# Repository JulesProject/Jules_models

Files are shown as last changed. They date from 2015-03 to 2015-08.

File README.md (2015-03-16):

# README

## Abstract
Jules is a project started in February 2015. The aim of this project is to design a robot to help elementary and kindergaten teachers in there everyday jobs. 

Jules is designed to be safe for kids, nice looking and usefull for their teachers. Jules must be suitable to kids from 5 to 9 years old and propose differents scenarios for them too.

## Folders Structure

The Models folder contains all SolidWorks models (created with SolidWorks 2013). The Printing models are STL files designed to be printed with 3D printers.

* README
* models
    * accessories 
        * arms
        * feet
            * first_edition
            * second_edition
        * tail  
    * body   
        * neck
        * ballast
    * electronics   
        * ballBearing1
        * dynamixels
    * head  
        * antenna
* printing
    * antenna  
    * arms  
    * body  
    * feet  
    * head  
    * neck
    * ballast
    * tail

## Components

The components listed here are components we designed our solution for. 
Not all the components are required to create a first version of the robot.

#### Head components
* Camera - [LogitechC920]
* Actuator Dynamixel RX-24f - [Dynamixel]
* Screen + TouchScreen - HDMI+VGA+2AV Controller Board VS-TY2662-V1 7 inch 800* 480  Lcd Panel AT070TN92 with Touch Screen  
    * USB Controller Card
    * USB Cable
* Speakers Monacor SPP-90 - [Speakers]
    * Audio amplifier - [Amplifier]
* Actuator to card transformer - [USB2Dynamixel]
* Electronic card + Heat sink - [BananaPi]

#### Body components
* Microphone - [Boya]
* Actuator - [Dynamixel]
* On/Off button
* Ultrasound card - HC-SR04

#### Other mendatory materials
* Ball bearing (x1) - [BallBearing1]
* Ball bearing (x2) - [BallBearing2]
* Power supply cable 12V 3A
* Power supply socket 
* Power converter (12V to 5V) - DC-DC 12V/ 24V to 5V 5A Step Down Regulator Module 25W Converter
* Power usb plug - Male B type Version 2.0 Micro USB Connector, 100 V ac, 1.8A
* SD card - 32Gb class 10
* Dynamixel cables - 4-pin
* ProtoBoard - [ProtoBoard]
* Resistor 470 ohm
* Resistor 330 ohm
* Wires
* Soldering iron
* Screws

[LogitechC920]:http://www.logitech.com/en-hk/product/hd-pro-webcam-c920
[Dynamixel]: http://en.robotis.com/index/product.php?cate_code=10101112&bbs_no=29#product_title
[Speakers]:http://www.monacor.co.uk/products/speakerbuilding-hifi-4/vnr/101150/
[USB2Dynamixel]:http://support.robotis.com/en/product/auxdevice/interface/usb2dxl_manual.htm
[BananaPi]:http://bananapi.com/index.php/component/content/article?layout=edit&id=73
[Boya]:http://www.boya-mic.com/products/show-394.html
[BallBearing1]:http://www.skf.com/uk/products/bearings-units-housings/ball-bearings/deep-groove-ball-bearings/single-row-deep-groove-ball-bearings/single-row/index.html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
[BallBearing2]:http://www.skf.com/uk/products/bearings-units-housings/ball-bearings/deep-groove-ball-bearings/single-row-deep-groove-ball-bearings/single-row/index.html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
[Amplifier]:https://learn.adafruit.com/adafruit-ts2012-2-8w-stereo-audio-amplifier/overview

## Printing

All the parts can be printed on a 3D printer with at least a 18x18x18cm plateau (originally designed to be printed with a Ultimaker printer). 

It is needed around 3kg of material to be able to print the full robot. 
Arms, feet, antenna, tail are designed to be printed in another color than the rest of the robot.

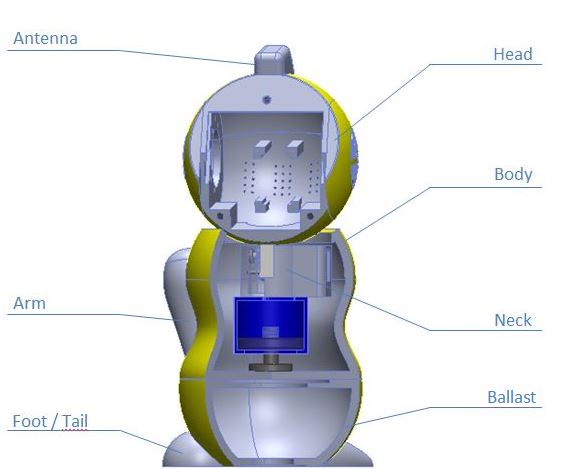
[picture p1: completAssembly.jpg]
Root complete Assembly


Two versions of the feet are available. For the second version, the tail file is needed as well to insure the stability of the robot.

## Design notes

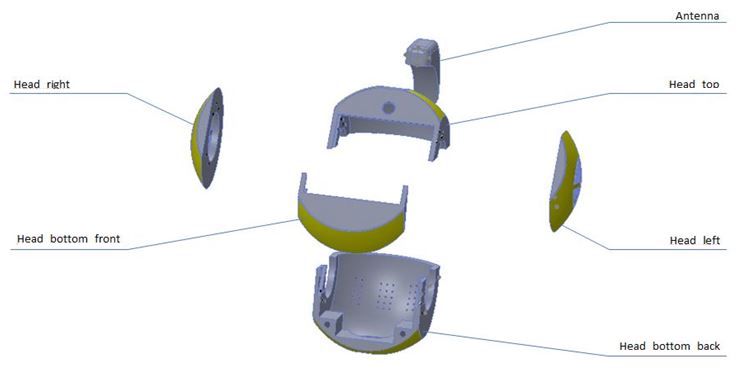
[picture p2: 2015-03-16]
models/head/head.JPG

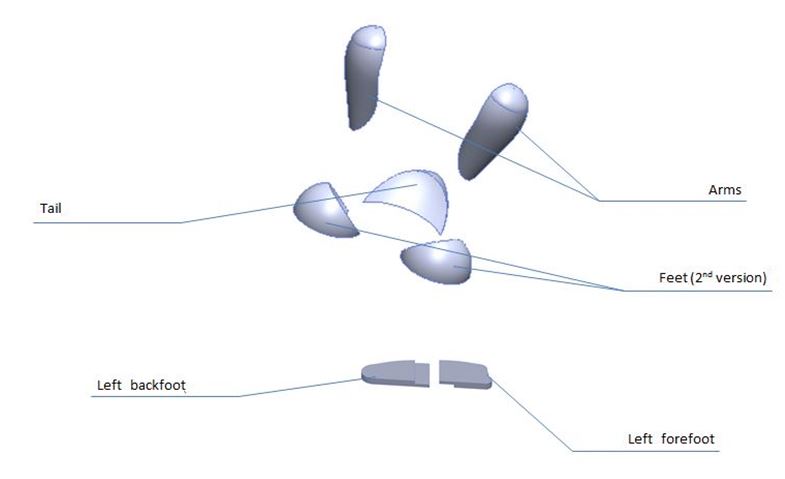
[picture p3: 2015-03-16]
models/accessories/accessories.JPG

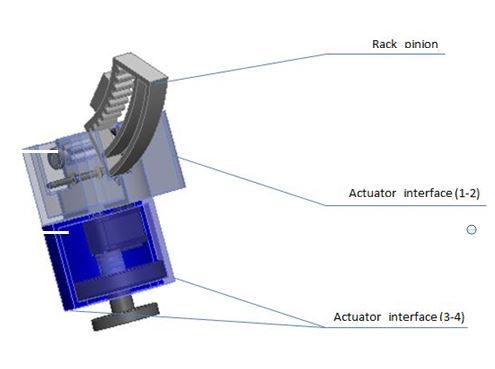
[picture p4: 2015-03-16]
models/body/neck/neck.JPG

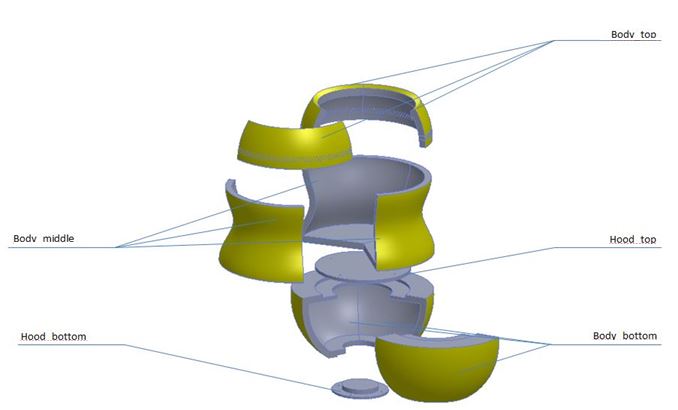
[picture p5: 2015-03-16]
models/body/body.JPG

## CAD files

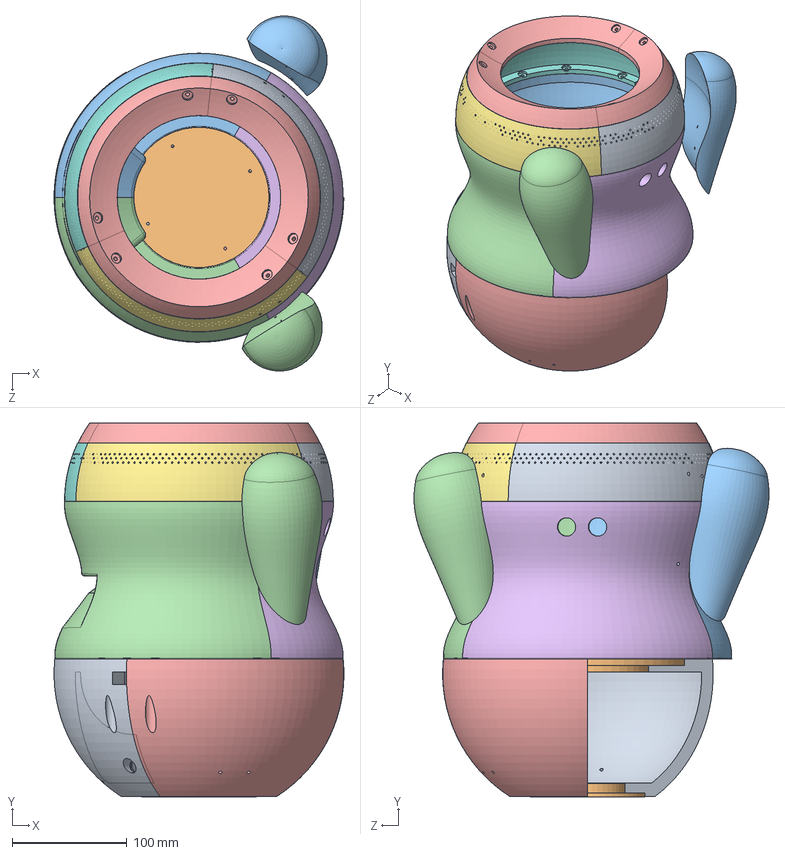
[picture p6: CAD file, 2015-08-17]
models/body/bodyAssembly.SLDASM
252.0 x 325.0 x 308.7 mm
body_bottom_back
hood_bottom
body_middle_handle_left
body_middle_handle_right
body_bottom_left
body_middle_front
body_top_left
body_top_middle
body_top_right
hood_top
right_arm
left_arm
body_top_hood x 3

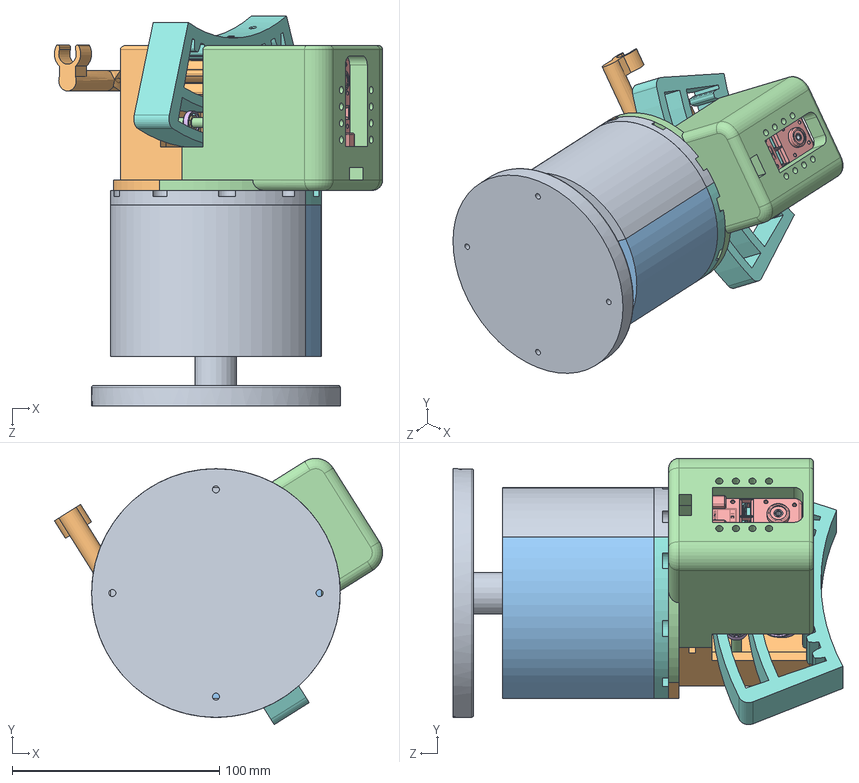
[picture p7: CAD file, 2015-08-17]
models/body/neck/neck.sldasm
158.4 x 128.5 x 188.2 mm
actuator_interface_3
actuator_interface_2
actuator_interface_4
actuator_interface_1
ASSY_DUMMY___^AX-18A
ASSY_GEAR-WHEEL___DUMMY^AX-18A
DX124_SCREW-COVER___^AX-18A x 4
099990987____^AX-18A x 2
DC04_B01_INSERT_M3^AX-18A
DC04_B01_HORN2_DUMMY^AX-18A
BHS_M2_6X8^AX-18A
neck_axis x 2
ball1 x 2
ball2 x 2
ball3 x 2
ball4 x 2
ball5 x 2
ball6 x 2
ball7 x 2
ball8 x 2
ball9 x 2
external_ring x 2
internal_ring x 2
rack_pinion
sprocket_2
sprocket_1
AX-12A-01
AX-12A-02
AX-12A-03
AX-12A-04
SetScrew x 4
M2.5 x 8
actuator_holder
actuator_axis
ball
ball_2
ball_3
ball_4
ball_5
ball_6
ball_7
ball_8
ball_9
ball_10
ball_11
external_bearing_ring
internal_bearing_ring
actuator_interface_3_handle
actuator_interface_4_handle
handle_microphone

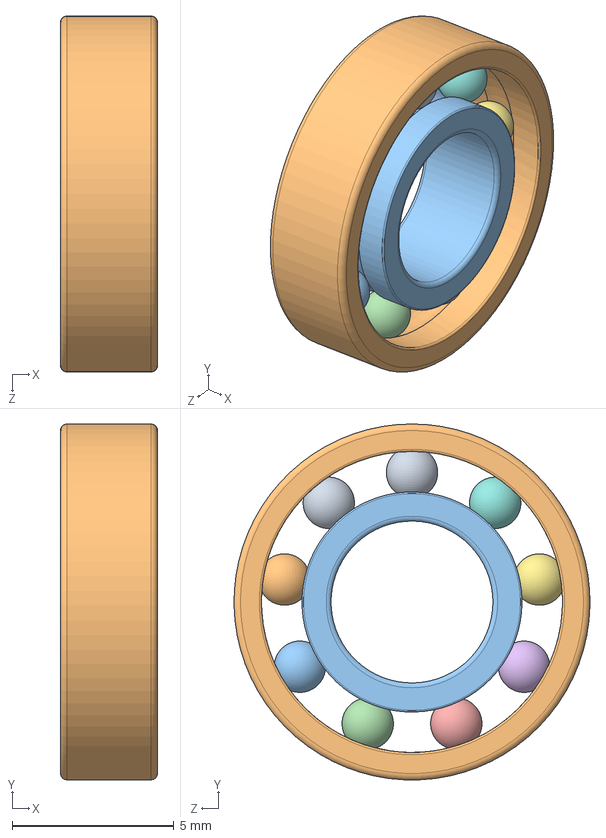
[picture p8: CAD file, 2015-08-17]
models/electronics/ballBearing1/ballBearing.SLDASM
3.00 x 11.0 x 11.0 mm
ball1
ball2
ball3
ball4
ball5
ball6
ball7
ball8
ball9
external_ring
internal_ring

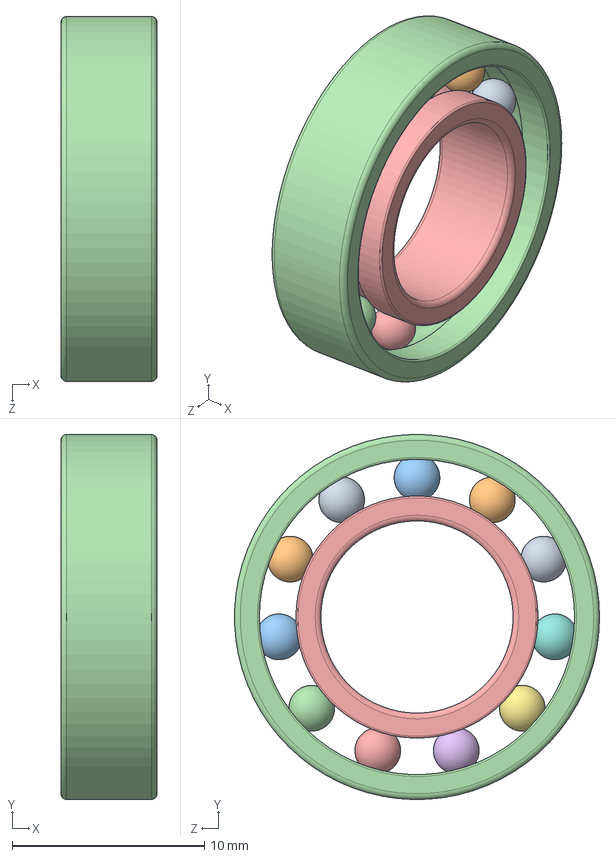
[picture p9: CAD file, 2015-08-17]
models/electronics/ballBearing2.sldasm
5.00 x 19.0 x 19.0 mm
ball
ball_2
ball_3
ball_4
ball_5
ball_6
ball_7
ball_8
ball_9
ball_10
ball_11
external_bearing_ring
internal_bearing_ring

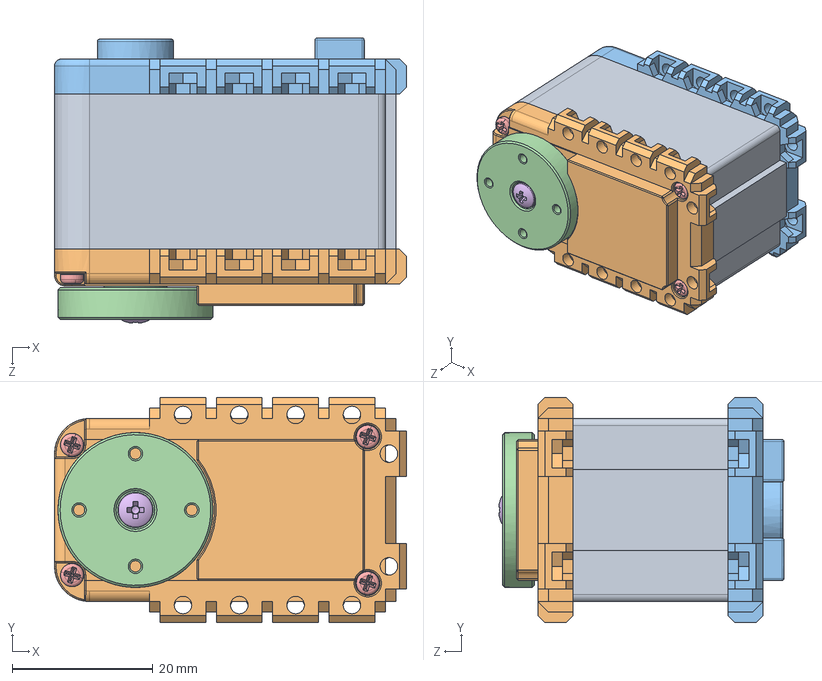
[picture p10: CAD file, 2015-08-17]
models/electronics/dynamixels/DYNAMIXEL AX-12A.SLDASM
50.0 x 32.0 x 40.5 mm
AX-12A-01
AX-12A-02
AX-12A-03
AX-12A-04
SetScrew x 4
M2.5 x 8

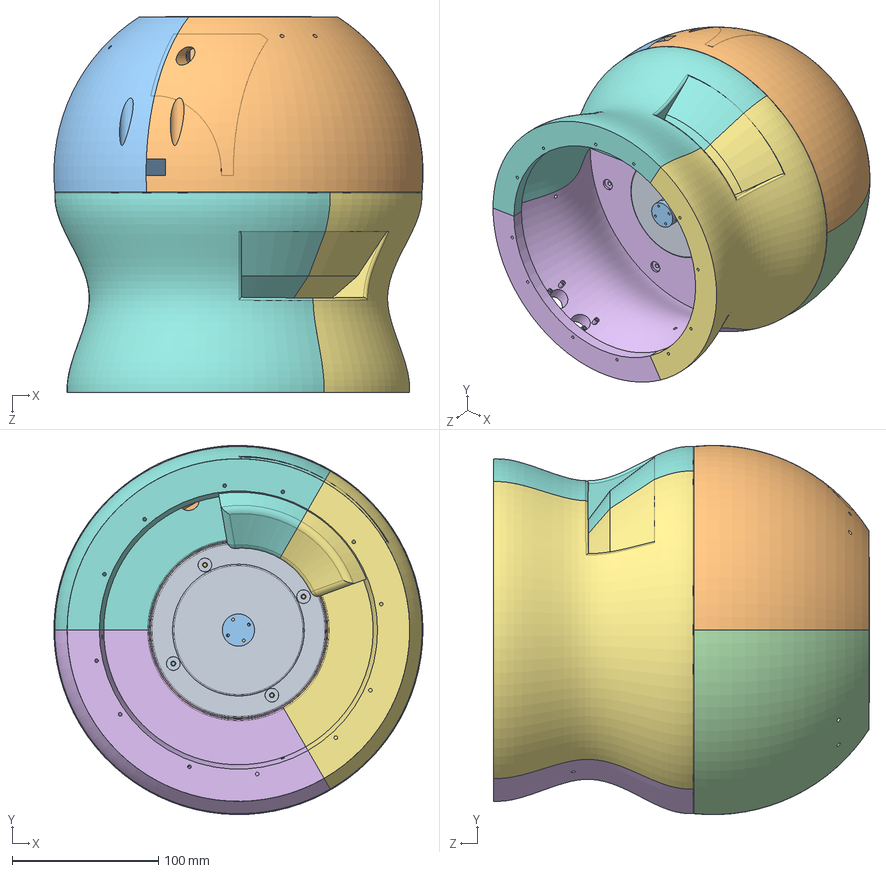
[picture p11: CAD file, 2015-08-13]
models/finalAssembly2.SLDASM
252.0 x 252.1 x 257.1 mm
hood_bottom
body_bottom_back
body_bottom_left
body_bottom_right
hood_top
body_middle_front
body_middle_handle_left
body_middle_handle_right
actuator_holder
sprocket_2
sprocket_1

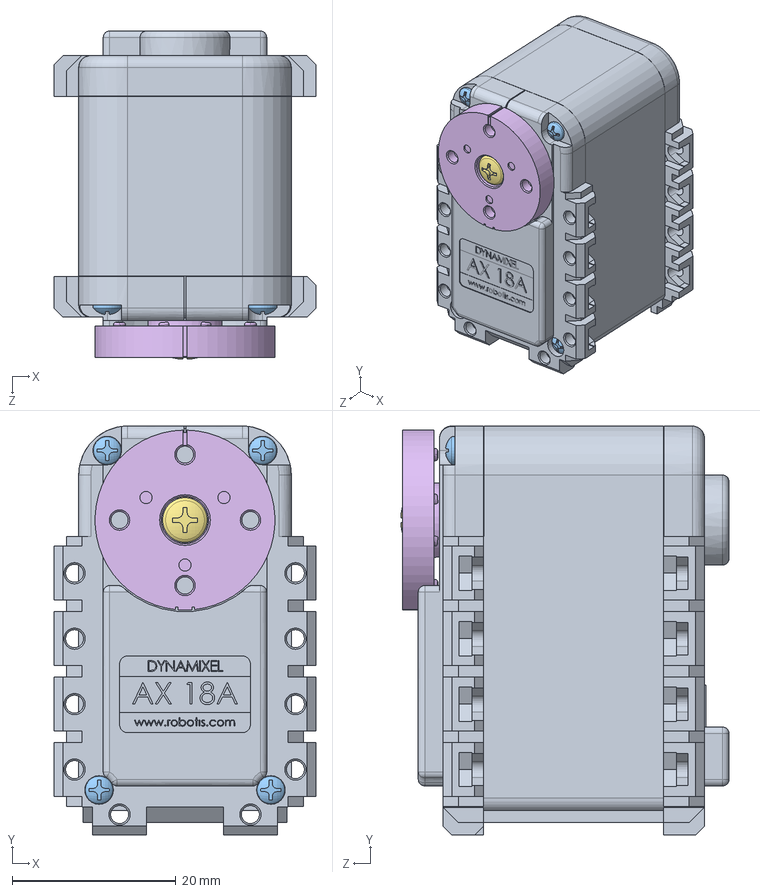
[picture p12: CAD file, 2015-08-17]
models/electronics/dynamixels/AX-18A.SLDASM
32.0 x 50.0 x 40.1 mm
ASSY_DUMMY___^AX-18A
ASSY_GEAR-WHEEL___DUMMY^AX-18A
DX124_SCREW-COVER___^AX-18A x 4
099990987____^AX-18A x 2
DC04_B01_INSERT_M3^AX-18A
DC04_B01_HORN2_DUMMY^AX-18A
BHS_M2_6X8^AX-18A

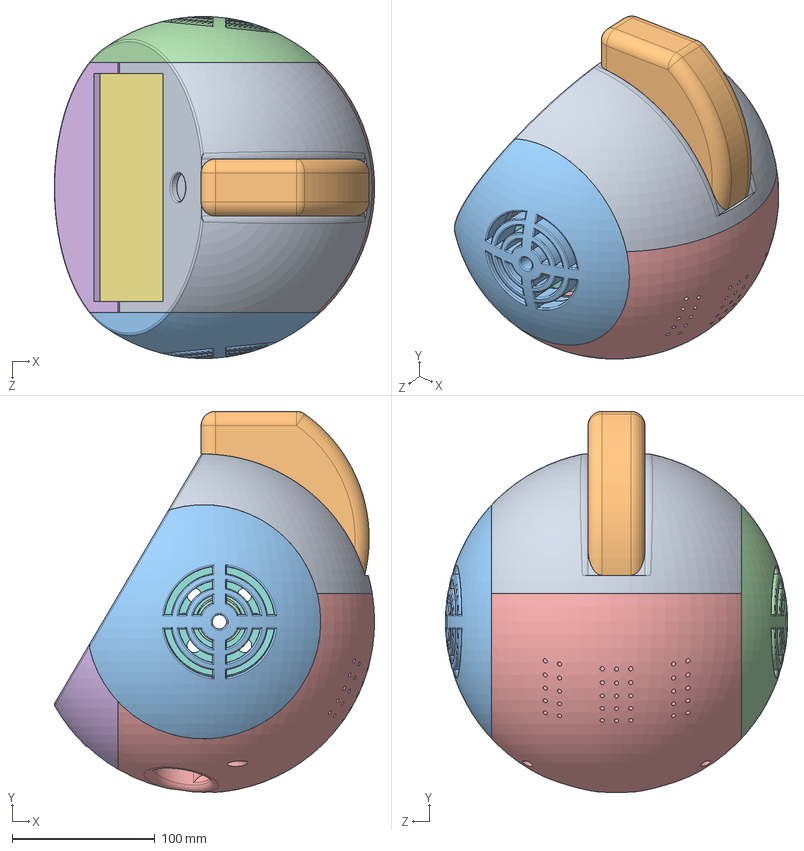
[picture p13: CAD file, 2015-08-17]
models/head/fullHead.SLDASM
224.5 x 267.4 x 239.9 mm
head_top
antenna
head_right
head_left
head_bottom_back
head_bottom_front
screen_ts
speaker_holder x 2
logitech_webcam
webcam_holder

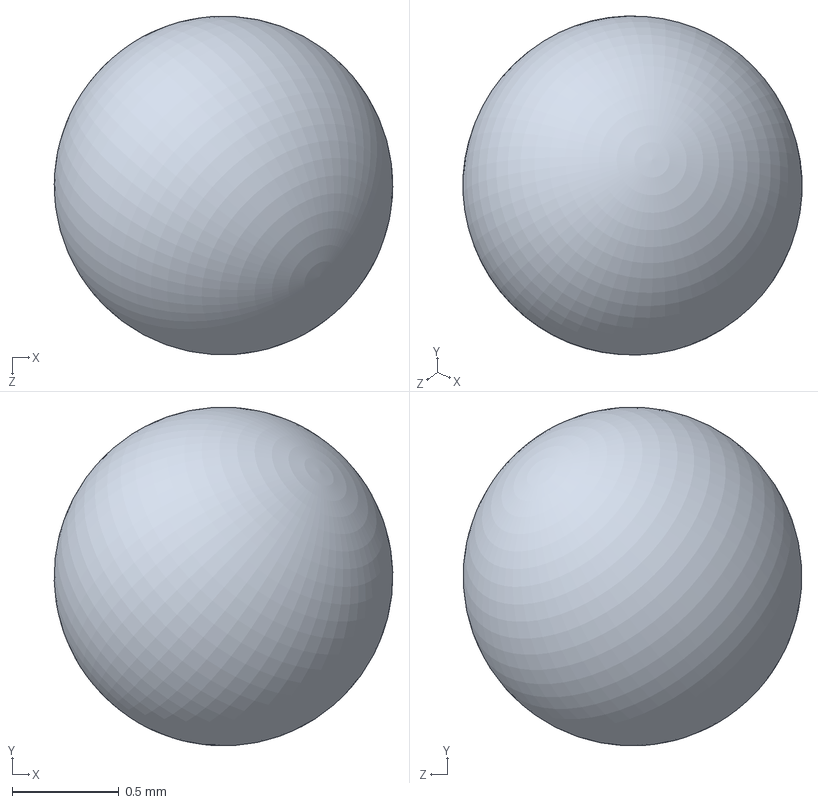
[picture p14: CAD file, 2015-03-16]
models/electronics/dynamixels/4_PART_618_5_PART3_in_ASM_618_5.sldprt
1.59 x 1.59 x 1.58 mm

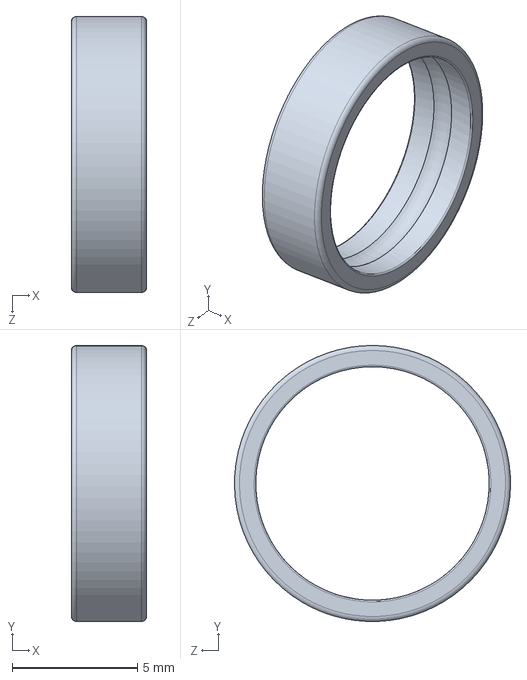
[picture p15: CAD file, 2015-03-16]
models/electronics/dynamixels/10_PART_618_5_PART3_in_ASM_618_5.sldprt
3.00 x 11.0 x 11.0 mm

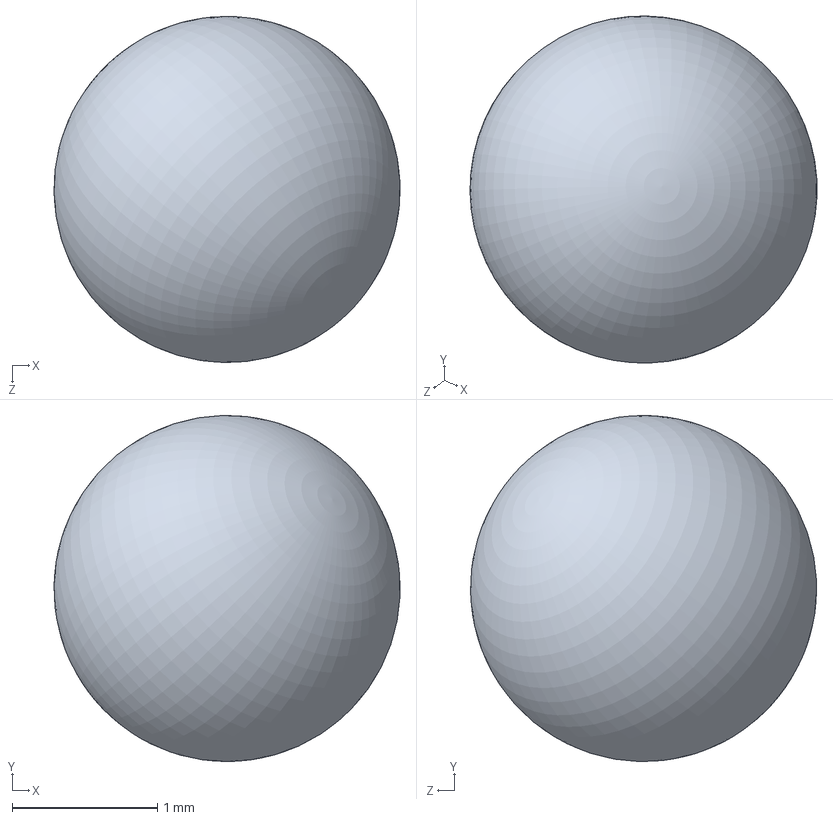
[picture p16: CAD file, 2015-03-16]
models/electronics/dynamixels/5_PART_61800_PART3_in_ASM_61800.sldprt
2.38 x 2.38 x 2.38 mm

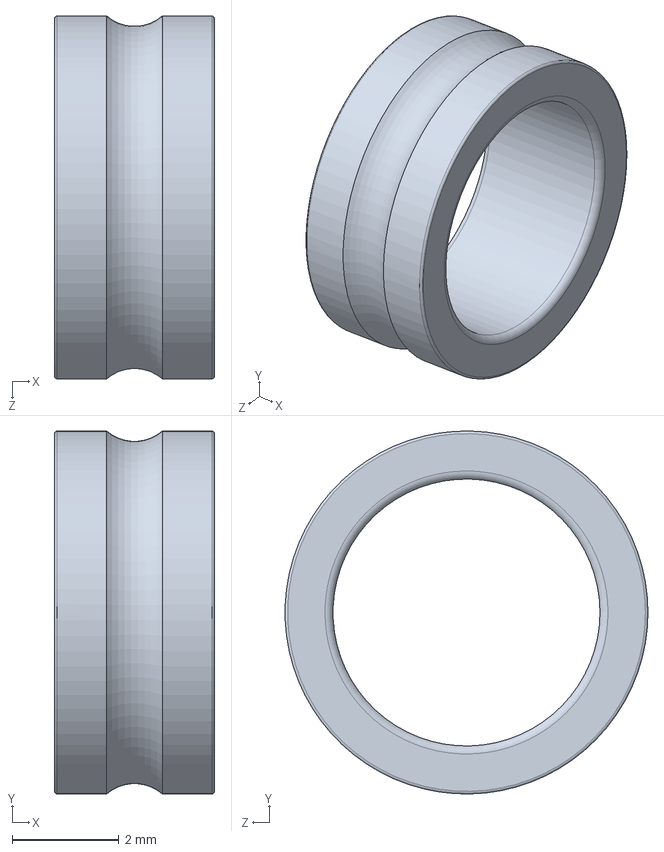
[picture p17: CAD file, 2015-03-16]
models/electronics/dynamixels/11_PART_618_5_PART3_in_ASM_618_5.sldprt
3.00 x 6.80 x 6.80 mm

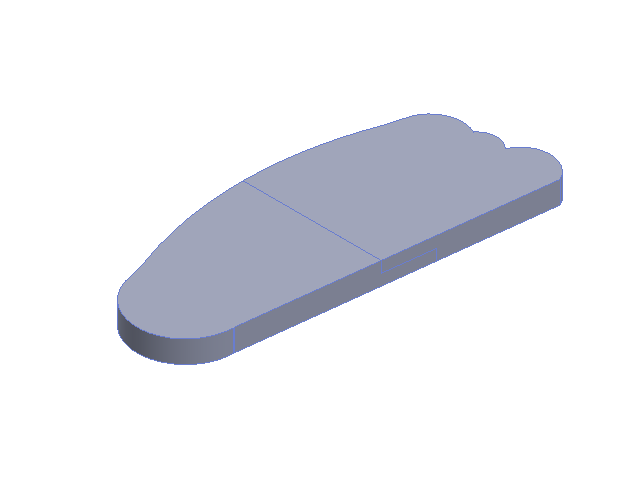
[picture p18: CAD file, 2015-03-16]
models/accessories/feet/first_edition/left_foot.SLDASM
left_forefoot
left_backfoot

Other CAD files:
models/electronics/dynamixels/2_PART_618_5_PART2_in_ASM_618_5.sldprt
models/electronics/dynamixels/1_PART_618_5_PART1_in_ASM_618_5.sldprt
models/electronics/dynamixels/7_PART_618_5_PART3_in_ASM_618_5.sldprt
models/electronics/dynamixels/4_PART_61800_PART3_in_ASM_61800.sldprt
models/electronics/dynamixels/6_PART_61800_PART3_in_ASM_61800.sldprt
models/accessories/arms/left_arm.SLDPRT
models/accessories/arms/right_arm.SLDPRT
models/accessories/feet/first_edition/left_backfoot.SLDPRT
models/accessories/feet/first_edition/left_forefoot.SLDPRT
models/accessories/feet/second_edition/left_foot.SLDPRT
models/accessories/feet/second_edition/right_foot.SLDPRT
models/accessories/tail/tail.SLDPRT
models/body/ballast/body_bottom_back.SLDPRT
models/body/ballast/body_bottom_left.SLDPRT
models/body/ballast/body_bottom_right.SLDPRT
models/body/ballast/hood_bottom.SLDPRT
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

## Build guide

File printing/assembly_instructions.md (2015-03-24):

# Instructions for assembly

Assembly video : 
[Assembly video](http://youtu.be/b8QJ62R7ehc)

## The body assembly

### The first version feet assembly

Need:
* Plastic parts:
* Backfoot x2
* Forefoot x2

First, take the forefoot and backfoot of one of your feet.
Screw the external screw of the foot from the bottom of this one.

Repeat with your second foot.

### The ballast assembly

Need: 
* Plastic parts:
* Body bottom x1
* Body bottom with switch and power supply cable x1
* Body bottom with internal hood x1
* Hood top x1
* Hood bottom x1
* Foot x2
* Electronics:
* Switch x1
* Power supply cable x1
* Power supply plug x1
* Other
* Bag food of iron x1

Take the body bottom with the holes for the switch and power supply plug.
Fix the switch and weld it.
Fix the power plug and weld it as well.

Take the body bottom with the internal hood and screw it on the right part of previous piece

Take the bottom hood and screw it on one of the body bottom top part.
Do the same with the two other bottom's parts.

Put the bag food of iron inside of the structure and screw the top hood to the structure.

Take one of your feet, return the ballast and screw it.
Repeat the same with the second foot.

### The middle body assembly

Need:
* Plastic parts:
* Ballast assembly x1
* Body front middle (with ultrasound holes) x1
* Body middle (with left handle) x1

Take the ballast assembly and screw one of the middle body on it. 
Repeat the same with the two other middle body parts.

### The neck assembly

Need:
* Plastic parts:
* Middle body assembly x1
* Neck x1
* Electronics:
* Dynamixel RX-24f x2
* Microphone x1

Take the middle body assembly and screw on it (in the middle of the structure, inside the middle parts), the neck.

### The middle body

Need:
* Plastic parts:
* Body assembly x1
* Body middle (with right handle) x2

Screw the two middle parts to the robot thanks to the holes in the back of it.

### The upper body assembly

Need:
* Plastic parts:
* Neck assembly
* Body top x3
* Body hood x3
* Arm x2
* Neck hood x1
* Electonics:
* Ultrasound card x1

Screw an arm to each of the body top parts.
Take the two body top parts and screw them together thanks to the two screws holes integrated.

Screw this structure to the whole assembly done before.

Plug the ultrasound card to the body top front and screw it.

Position the body top front on the top of the structure, next to the two other body top parts.
Don't forget to make all the cables getting out of the neck.
Add the neck hood on top of it and screw the structure together.

## The head assembly 

### The top of the head

Need: 
* Plastic parts:
* Forehead x1
* Antenna x1
* Camera hood x1
* Electronics:
* Camera x1

Take the forehead and screw the antenna to it.

Take the camera and place it in the forehead. Fix it thanks to the hood to the forehead.

### The sides of the head

Need:
* Plastic parts:
* Top assembly x1
* Head side x2

Screw each side part to the top assembly.

### The back head

Need:
* Plastic parts:
* Sides assembly x1
* Back of the head x1
* Speaker hood x2
* Body assembly x1
* Electronics:
* Speaker x2
* Bananapi card x1
* Amplifier x1
* USB2Dynamixel x1

Place the speakers in their holes in the head. Assemble the back of the head to the rest of the assembly thanks to the hoods. 

Take the amplifier and plug the speakers on it.

Take the bananapi card, plug the amplifier on it and the camera.

Plug the Dynamixel to the usb2dynamixel module throught the neck hole of the head.

Take the cables from the body (ultrasound, microphone and power) and make them go throught the head neck.
Plug those cables to the card.

Screw the card in the head.

### The chin

Need: 
* Plastic parts:
* Back head assembly x1
* Chin x1
* Eletronics:
* Screen x1

Plug the screen to the card.
Slip the screen to the head.

Slip the chin and screw it from the back of the head (through the body middle parts missing).

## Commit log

2015-03-16 First version of models
    [10_PART_61800_PART3_in_ASM_61800.sldprt, 10_PART_618_5_PART3_in_ASM_618_5.sldprt, 11_PART_61800_PART3_in_ASM_61800.sldprt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]
2015-03-20 Second version of printing with holes and complete assembly
    [actuator_axis.STL, actuator_holder.STL, actuator_interface_1.STL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]
2015-03-24 Models version with all holes for assembling
    [DYNAMIXEL AX-12A.SLDASM, UltraSonic.sldprt, actuator_axis.SLDPRT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]
2015-03-24 Add link for assembly video
2015-07-07 some updates
    [AX-12A-01.sldprt, AX-12A-02.sldprt, AX-12A-03.sldprt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]
2015-07-07 starting new assembly
    [body_bottom_right.SLDPRT, finalAssembly2.SLDASM]
2015-08-11 WIP: fixes
    fixes speaker handler
    fixes olimex handler
    fixes actuator interface 1
    fixes sproket1
    fixes connectors in ballast
    [actuator_interface_1.SLDPRT, body_bottom_back.SLDPRT, body_middle_handel_right.SLDPRT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]
2015-08-13 wip: clean up
    [AX-18A.SLDASM, Assemblage3.sldasm, DYNAMIXEL AX-12A.SLDASM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]
2015-08-17 wip: fixes
    [AX-18A.SLDASM, Assemblage3.sldasm, DYNAMIXEL AX-12A.SLDASM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]
2015-08-17 wip: add cable holes
    [actuator_interface_1.SLDPRT, actuator_interface_2.SLDPRT, actuator_interface_3_handle.SLDPRT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]
2015-08-17 wip: the stl files
    [actuator_interface_1.STL, actuator_interface_2.STL, actuator_interface_3_handle.STL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]
